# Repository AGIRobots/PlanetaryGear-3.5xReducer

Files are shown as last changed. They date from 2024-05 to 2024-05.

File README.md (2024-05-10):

# PlanetaryGear-3.5xReducer for CyberGear 



Contains the design, documentation, and implementation details for an additional gearbox compatible with the CyberGear motor. It enhances the CyberGear motor's functionality with extra reduction capabilities, making it suitable for applications requiring higher torque.

Detailed operational instructions, assembly procedures, and simple torque tests are available in our YouTube video linked below. This video also provides practical insights into the assembly and testing processes.

https://youtu.be/O-cvOlKmTHc
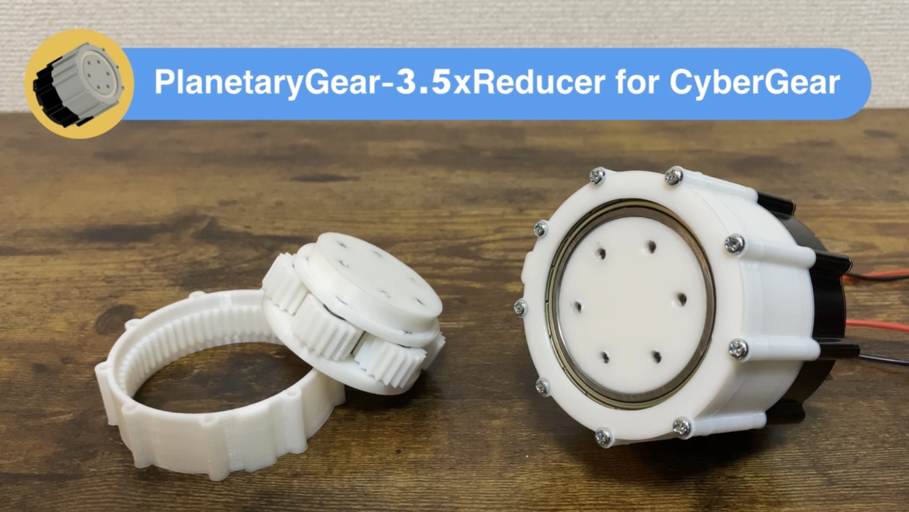
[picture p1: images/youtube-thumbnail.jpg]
(https://youtu.be/O-cvOlKmTHc)


## Technical Specifications
* Internal Gear Teeth: 60
* Sun Gear Teeth: 24
* Planet Gear Teeth: 18
* Reduction Ratio: 1:3.5
## Performance
The experimental torque is confirmed up to 35Nm, though calculations suggest that the gearbox could theoretically output up to 42Nm, compared to the CyberGear's rated maximum torque of 12Nm.
## 3D Printing Requirements
Parts required to be 3D printed are stored in the 3d_models folder. Notably, the file PlanetGear.stl needs to be printed six times.
## Parts List
The following parts must be purchased for assembly:
* CyberGear Main Unit: x1
* Bearings (6810ZZ): x1
* Bearings (HK0612): x6
* Cylindrical Pin (M6, 20mm): x6
* Thrust Bearing (AXK3552+2AS): x1
* Insert Nut (M4x8x6.4mm): x6
* Screws (M3x45mm): x9
* Screws (M3x15mm): x3
* Screws (M4x10mm): x3

## Comprehensive Assembly Overview
For a full understanding of all the components that need to be assembled, including those printed from the 3d_models directory, refer to the image below:
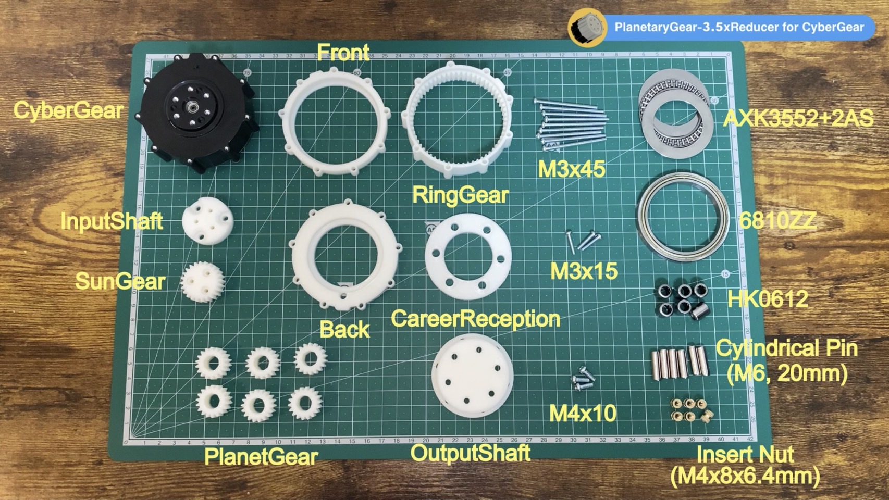
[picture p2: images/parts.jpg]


## Software for Operational Testing
The operational testing was conducted using a program available under the MIT License, which can be found here: CyberGear M5 Program (https://github.com/project-sternbergia/cybergear_m5).

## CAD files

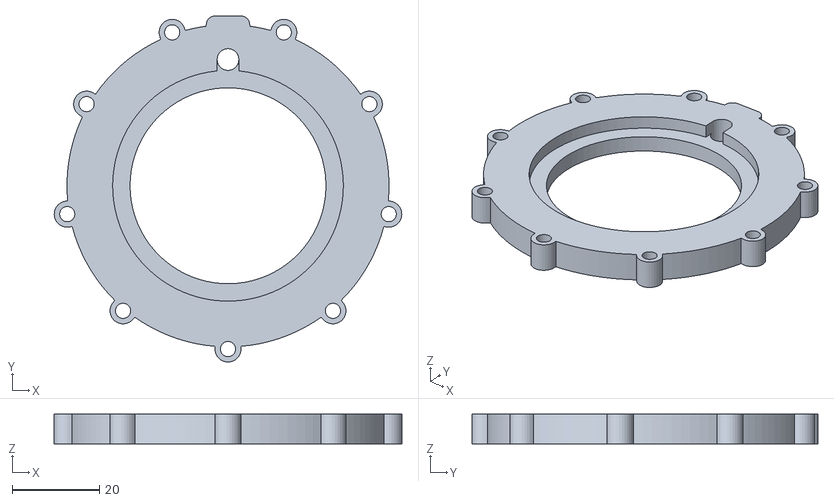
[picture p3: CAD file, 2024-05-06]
3d_models/Back.stl
79.8 x 79.5 x 6.78

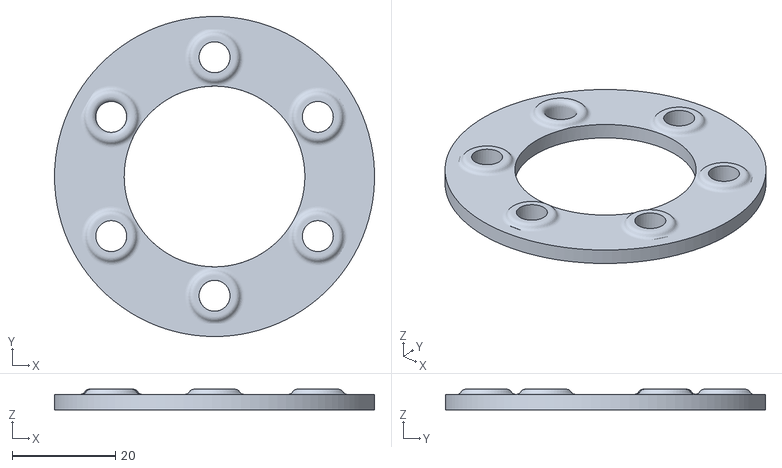
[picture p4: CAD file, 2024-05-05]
3d_models/CareerReception.stl
62.0 x 62.0 x 4.00

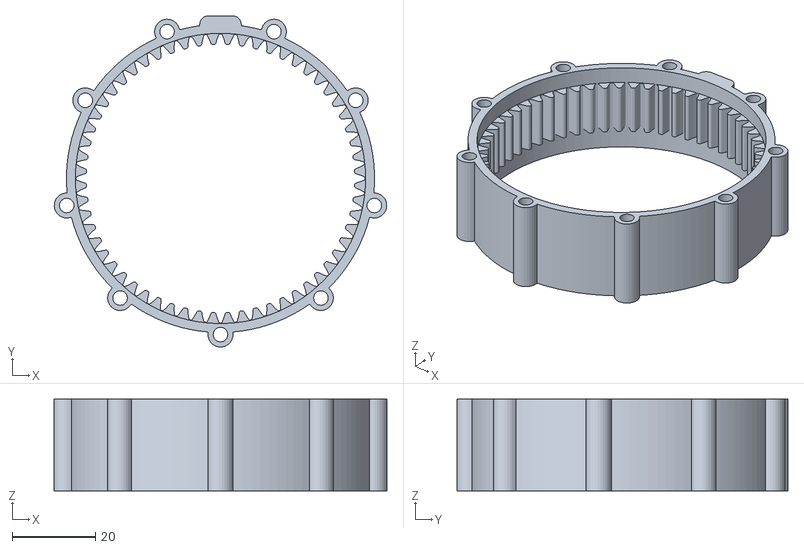
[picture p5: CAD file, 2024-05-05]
3d_models/RingGear.stl
79.8 x 79.5 x 22.0

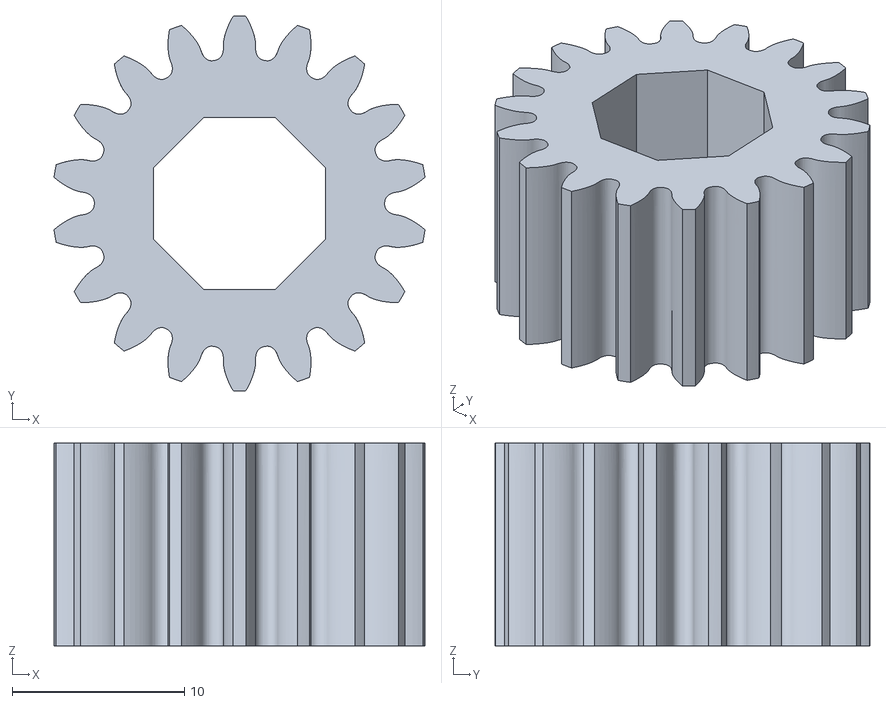
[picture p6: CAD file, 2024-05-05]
3d_models/PlanetGear.stl
21.6 x 21.8 x 11.8

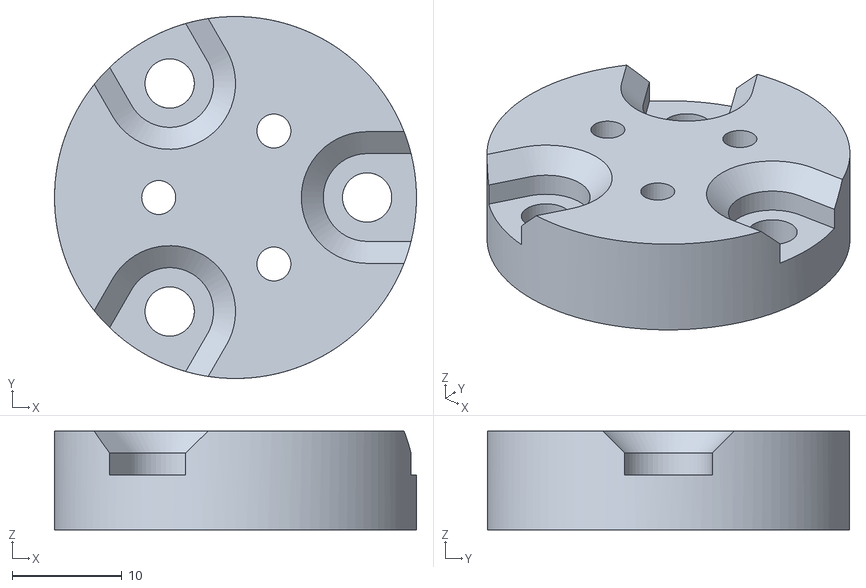
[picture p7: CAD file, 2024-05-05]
3d_models/InputShaft.stl
33.0 x 33.0 x 9.00

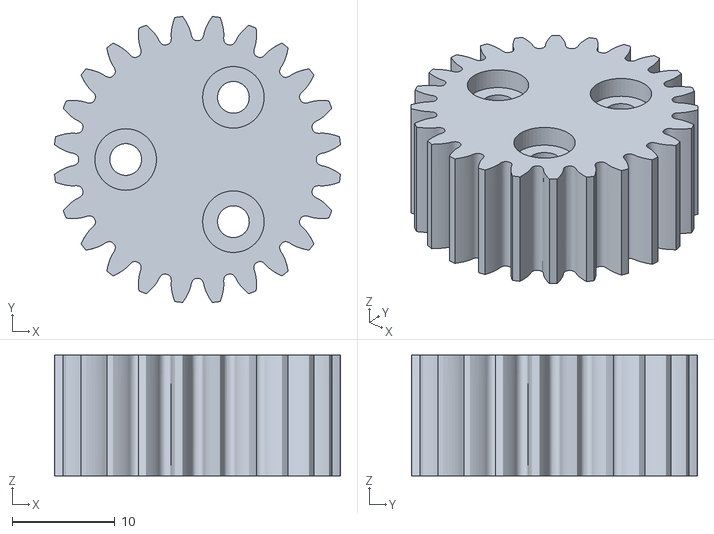
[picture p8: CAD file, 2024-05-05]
3d_models/SunGear.stl
27.9 x 27.9 x 11.8

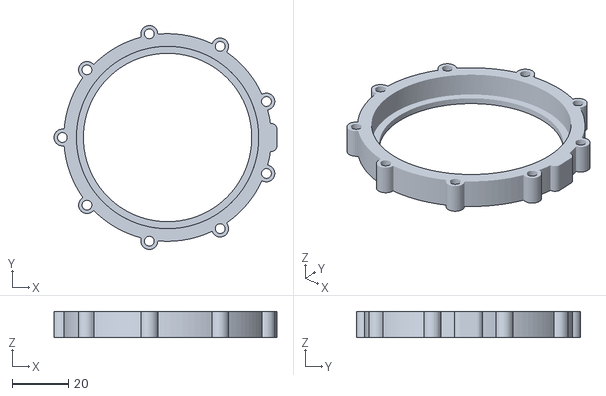
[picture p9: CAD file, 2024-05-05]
3d_models/Front.stl
79.5 x 79.8 x 9.44

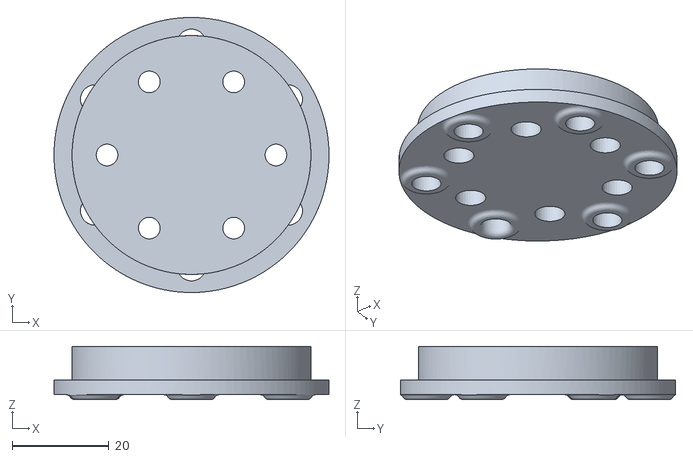
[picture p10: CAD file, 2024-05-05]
3d_models/OutputShaft.stl
57.0 x 57.0 x 11.0

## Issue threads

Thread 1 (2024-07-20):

Suggestion to publish editable 3D-CAD data.

shiba-8ro, 2024-07-20:
@AGIRobots I have started making PlanetaryGear-3.5xReducer, but I am having trouble with an issue specific to the 3D printer slicer software I am using. It depends on the resolution of the STL data. So I want to export the STL data at any resolution I want. Also, I would like to DfAM the data for better 3D printing results. Is it possible for you to publish the data in STEP format?
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

AGIRobots, 2024-07-20:
@shiba-8ro
Thank you for your suggestion. I have added the data under the 3d_models folder as PlanetaryGear-3.5xReducer.step, please feel free to use it.

shiba-8ro, 2024-07-22:
@AGIRobots
Thank you. You shall close this issue.

shiba-8ro, 2024-07-22:
@AGIRobots
Thank you. I closed this issue.

Closed 2024-07-22.

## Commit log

2024-05-05 Added 3d models
    [Back.stl, CareerReception.stl, Front.stl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]
2024-05-05 Deteted CareerReception.stl
    [CareerReception.stl]
2024-05-05 Added fixed CareerReception.stl
    [CareerReception.stl]
2024-05-06 Deleted Back.stl
    [Back.stl]
2024-05-06 Added fixed Back.stl
    [Back.stl]
